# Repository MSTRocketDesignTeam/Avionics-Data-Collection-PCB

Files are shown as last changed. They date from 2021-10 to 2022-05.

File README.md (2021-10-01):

# Overview

This repository contains the PCB design files and accompanying firmware for the Data Collection Board of the S&T Rocket Design Team's SRAD Avionics system.

## Purpose and Motivation
The goal of this project is to create flight-rate PCBs that can collect information about the teams rockets as they are launched.

## Inspirations

Initial developments of this board are to be more or less a direct replacement for a Telemetrum V3, with features and design optimizations to be implemented in future revisions.

A [Telemetrum V3](https://altusmetrum.org/TeleMetrum/) is an amateur rocketry telemetry solution from [Altus Metrum](https://altusmetrum.org/index.html).

[Signal](https://bps.space/signal/) from [BPS.Space](https://bps.space/) is a flight computer first and a data collection solution second. It is designed to stream data to the ground station, although it is likely insufficient for the large 10-30k ft class rockets that our team constructs.

There is also a really cool KiCad tutorial around making a small thumb drive sized pcb with an STM32, RF, and USB components. The link is [here on youtube by Phil's Lab](https://www.youtube.com/watch?v=14_jh3nLSsU) and is a great tutorial on using circuit design software and the process/approach you go through making something like this. Highly recommended to watch and maybe take some notes on, and a pretty solid start for our telemetry board.

# Features

#### Physical

#### Primary Components

#### Sensors

#### Data

#### Power

# Companion Documentation

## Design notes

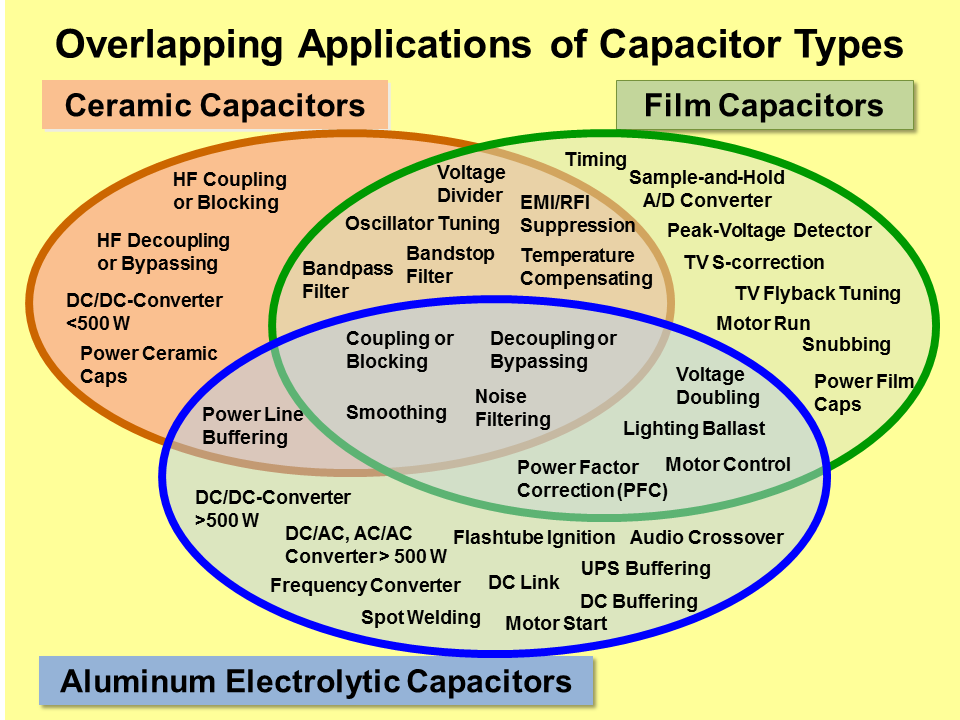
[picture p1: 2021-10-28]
Documentation/Capacitor_Uses.png

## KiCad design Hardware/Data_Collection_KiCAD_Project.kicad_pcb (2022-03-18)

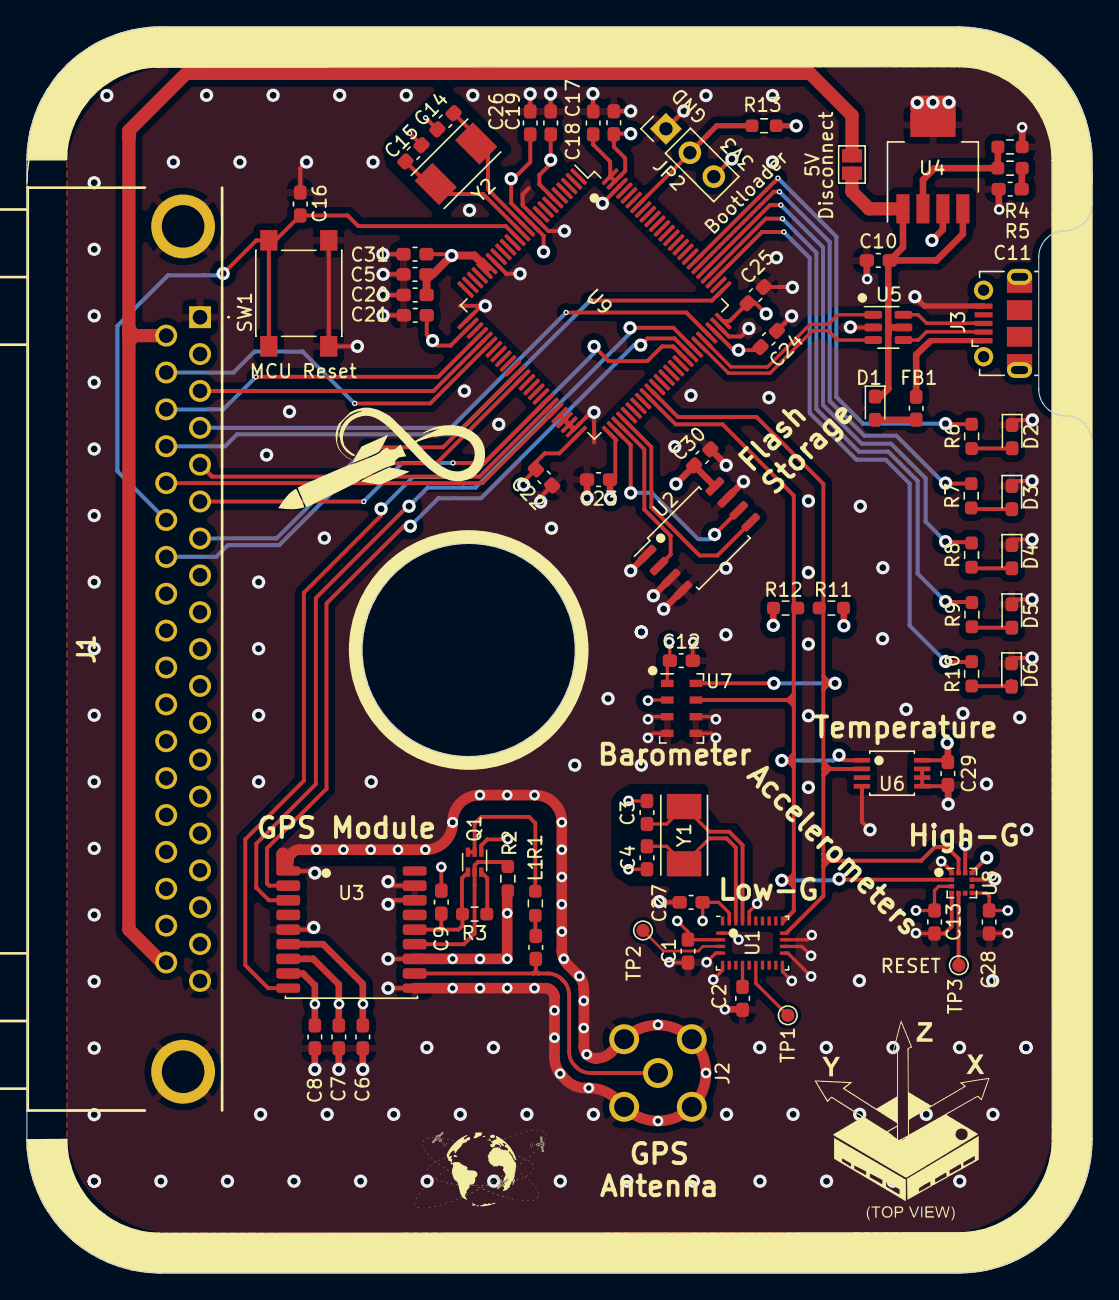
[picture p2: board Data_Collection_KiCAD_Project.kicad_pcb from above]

Board: 4 copper layers, 80.0 x 93.6 mm, 73 parts (0 on the bottom side), 56 nets.

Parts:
C1, C2, C3, C4, C10, C13, C27, C28, C29, C30: 0.1uF; C_0603_1608Metric_Pad1.08x0.95mm_HandSolder
C5, C6, C7, C8, C12, C16, C18, C19, C20, C21, C22, C23, C24, C25: 100nF; C_0603_1608Metric_Pad1.08x0.95mm_HandSolder
C9: 1nF; C_0603_1608Metric_Pad1.08x0.95mm_HandSolder
C11, C17, C26, C31: 1uF; C_0603_1608Metric_Pad1.08x0.95mm_HandSolder
C14, C15: 30pF; C_0603_1608Metric_Pad1.08x0.95mm_HandSolder
D1: D_Schottky_Small; D_0603_1608Metric_Pad1.05x0.95mm_HandSolder
D2, D4, D6: Red; LED_0603_1608Metric_Pad1.05x0.95mm_HandSolder
D3, D5: Grn; LED_0603_1608Metric_Pad1.05x0.95mm_HandSolder
FB1: Ferrite_Bead_Small; C_0603_1608Metric_Pad1.08x0.95mm_HandSolder
J1: L717SDC37P1ACH4F
J2: Conn_Coaxial; SMA_Molex_73251-2200_Horizontal
J3: 10118192-0001LF; USB_Micro-B_Molex-105017-0001
JP1: 5V Disconnect; SolderJumper-2_P1.3mm_Open_Pad1.0x1.5mm
JP2: Debug Jumper; PinHeader_1x03_P2.54mm_Vertical
L1: 27nH; C_0603_1608Metric_Pad1.08x0.95mm_HandSolder
Q1: SI1040X-T1-GE3; SOT-563
R1, R2: 10k; R_0603_1608Metric_Pad0.98x0.95mm_HandSolder
R3: 100k; R_0603_1608Metric_Pad0.98x0.95mm_HandSolder
R4: 390; R_0603_1608Metric_Pad0.98x0.95mm_HandSolder
R5: 240; R_0603_1608Metric_Pad0.98x0.95mm_HandSolder
R6, R7, R8, R9, R10: 820; R_0603_1608Metric_Pad0.98x0.95mm_HandSolder
R11, R12, R13: 4.7k; R_0603_1608Metric_Pad0.98x0.95mm_HandSolder
SW1: MCU Reset; SW_SPST_PTS645
TP1, TP2, TP3: Debug Pad; TestPoint_Pad_D1.0mm
U1: BNO055; LGA-28_5.2x3.8mm_P0.5mm
U2: W25Q32JVSS; SOIC-8_5.23x5.23mm_P1.27mm
U3: MAX-8Q; ublox_MAX
U4: LP38692MPX-ADJ; SOT-223-5
U5: USBLC6-2SC6; SOT-23-6
U6: MIC184YMM-TR
U7: MS5607-02BA; LGA-8_3x5mm_P1.25mm
U8: KX134-1211; LGA-12_2x2mm_P0.5mm
U9: STM32L562VET6Q; LQFP-100_14x14mm_P0.5mm
Y1: 32.768kHz; XTAL_ABM7-32.000MHZ-D2Y-T
Y2: 32MHz; XTAL_ABM7-32.000MHZ-D2Y-T

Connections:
+3V3: C1.2, C5.1, C6.1, C7.1, C8.1, C12.1, C13.1, C17.1, C18.1, C19.1, C20.1, C21.1, C22.1, C23.1, C24.1, C25.1, C26.1, C27.2, C28.1, C29.1, C30.1, C31.1, J1.2, J1.18, JP2.3 (B), R11.2, R12.2, R13.1, U1.3 (VDD), U1.28 (VDDIO), U2.8 (VCC), U3.6 (V_BCKP), U3.7 (VCC_IO), U3.8 (VCC), U4.3 (VOUT), U6.8 (VDD), U7.1 (VDD), U7.2 (PS), U8.3 (IO_VDD), U8.7 (VDD), U8.10 (~CS), U9.6 (VBAT), U9.11 (VDD), U9.20 (VREF+), U9.21 (VDDA), U9.27 (VDD), U9.50 (V15SMPS_1), U9.51 (VDD), U9.73 (VDDUSB), U9.75 (VDD), U9.99 (V15SMPS_2), U9.100 (VDD)
+5V: C10.1, D1.1 (K), JP1.1 (A), U4.1 (EN), U4.4 (VIN), U5.5 (VBUS)
/37 Pin DSUB Bus/Dsub_5v: J1.20, J1.37, JP1.2 (B)
/ABORT_1: J1.7, U9.37 (PE9)
/ABORT_2: J1.26, U9.38 (PE10)
/ALERT_EN: J1.6, U9.43 (PE15)
/ALERT_SCL: J1.5, U9.44 (PB10)
/ALERT_SDA: J1.24, U9.45 (PB11)
/BNO055/~BNO055_BTL: TP2.1, U1.4 (~BOOT_LOAD_PIN)
/BNO055/~BNO055_RESET: TP1.1, U1.11 (~RESET)
/FLASH_CLK: U2.6 (CLK), U9.52 (PB13)
/FLASH_MISO: U2.2 (DO(IO1)), U9.53 (PB14)
/FLASH_MOSI: U2.5 (DI(IO0)), U9.54 (PB15)
/GPS_RX: U3.3 (RXD), U9.69 (PA10)
/GPS_TX: U3.2 (TXD), U9.68 (PA9)
/KX134-1211/KX134_INT1: TP3.1, U8.5 (INT1)
/MAX-8Q/GPS_ANT_NET: J2.1 (In), L1.2, U3.11 (RF_IN)
/MAX-8Q/GPS_LNA_EN: Q1.5 (G1), R2.1, U3.13 (LNA_EN)
/MAX-8Q/GPS_VCC_RF: C9.1, Q1.4 (S2), R3.2, U3.14 (VCC_RF)
/NRST: C16.1, J1.25, SW1.1, U9.14 (NRST)
/SENSOR_SCL: R11.1, U1.19 (COM1), U6.2 (CLK), U7.8 (SCLK), U8.12 (SCLK/SCL), U9.60 (PD13)
/SENSOR_SDA: R12.1, U1.20 (COM0), U6.1 (DATA), U7.7 (SDI/SDA), U8.2 (SDI/SDA), U9.59 (PD12)
/SWCLK: J1.23, U9.76 (PA14)
/SWDIO: J1.4, U9.72 (PA13)
/TELEMETRY_MISO: J1.3, U9.30 (PA6)
/TELEMETRY_MOSI: J1.21, U9.31 (PA7)
/TELEMETRY_SCK: J1.22, U9.29 (PA5)
/USB Connector and ESD/USB_CONN_D+: J3.3, U5.6 (I/O1)
/USB Connector and ESD/USB_CONN_D-: J3.2, U5.4 (I/O2)
/USB_D+: U5.1 (I/O1), U9.71 (PA12)
/USB_D-: U5.3 (I/O2), U9.70 (PA11)
/~GPS_RESET: U3.9 (~RESET), U9.67 (PA8)
GND: C1.1, C2.1, C3.1, C4.1, C5.2, C6.2, C7.2, C8.2, C9.2, C10.2, C11.2, C12.2, C13.2, C14.2, C15.2, C16.2, C17.2, C18.2, C19.2, C20.2, C21.2, C22.2, C23.2, C24.2, C25.2, C26.2, C27.1, C28.2, C29.2, C30.2, C31.2, D2.1 (K), D3.1 (K), D4.1 (K), D5.1 (K), D6.1 (K), J1.1, J1.19, J1.MH1, J1.MH2, J2.2 (Ext), J3.5, JP2.1 (A), Q1.1 (S1), R2.2, R4.2, SW1.2, U1.2 (GND), U1.5 (PS1), U1.6 (PS0), U1.15 (GNDIO), U1.16 (GNDIO), U1.17 (COM3), U1.18 (COM2), U1.25 (GNDIO), U2.1 (~CS), U2.3 (IO2), U2.4 (GND), U2.7 (IO3), U3.1 (GND), U3.5 (EXTINT), U3.10 (GND), U3.12 (GND), U3.16 (SDA), U3.17 (SCL), U4.5 (GND), U5.2 (GND), U6.4 (GND), U6.5 (A2/T1), U6.6 (A1), U6.7 (A0), U7.3 (GND), U7.4 (CSB), U7.5 (CSB), U7.6 (SDO), U8.1 (SDO/ADDR), U8.4 (TRIG), U8.9 (GND), U8.11 (NC), U9.10 (VSS), U9.19 (VREF-/VSSA), U9.26 (VSS), U9.46 (VDDSMPS), U9.47 (VLXSMPS), U9.48 (VSSSMPS), U9.49 (VSS), U9.74 (VSS), U9.98 (VSS)
unnamed: C2.2, U1.9 (CAP)
unnamed: C3.2, U1.26 (XOUT32), Y1.1
unnamed: C4.2, U1.27 (XIN32), Y1.2
unnamed: C11.1, R5.1
unnamed: C14.1, U9.12 (PH0), Y2.1
unnamed: C15.1, U9.13 (PH1), Y2.2
unnamed: D1.2 (A), FB1.1
unnamed: D2.2 (A), R6.1
unnamed: D3.2 (A), R7.1
unnamed: D4.2 (A), R8.1
unnamed: D5.2 (A), R9.1
unnamed: D6.2 (A), R10.1
unnamed: FB1.2, J3.1
unnamed: L1.1, R1.2
unnamed: Q1.2 (D2), Q1.3 (D2), R1.1
unnamed: Q1.6 (D1), R3.1
unnamed: R4.1, R5.2, U4.2 (ADJ)
unnamed: R10.2, U9.78 (PC10)
unnamed: R9.2, U9.79 (PC11)
unnamed: R8.2, U9.80 (PC12)
unnamed: R7.2, U9.81 (PD0)
unnamed: R6.2, U9.82 (PD1)
unnamed: JP2.2 (C), R13.2, U9.94 (PH3)

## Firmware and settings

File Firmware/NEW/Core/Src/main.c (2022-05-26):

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
/* Includes ------------------------------------------------------------------*/
#include "main.h"

 I2C_HandleTypeDef hi2c4;

void SystemClock_Config(void);
static void MX_GPIO_Init(void);
static void MX_I2C4_Init(void);
/**
  * @brief  The application entry point.
  * @retval int
  */
int main(void)
{
  /* USER CODE BEGIN 1 */

	HAL_StatusTypeDef i2c;
	const uint8_t MIC184_ADDR = 0x48 << 1;
	const uint8_t MIC184_CMD_REG = 0x01;
	const uint8_t MS5607_ADDR = 0x77 << 1;
	const uint8_t KX134_ADDR = 0x1E << 1;
	const uint8_t BNO055_ADDR = 0x28 << 1;


	uint8_t buf[1];
	uint8_t tmpBuf[3];
	uint8_t addr;
	uint8_t validAddr[20];
	uint8_t addrIndex = 0;


	/*
	HAL_StatusTypeDef i2c;
	uint8_t buf[1];
	const uint8_t BMP180_ADDR = 0x77 << 1; //7 bit addr?
	*/

  /* USER CODE END 1 */

  /* MCU Configuration--------------------------------------------------------*/

  /* Reset of all peripherals, Initializes the Flash interface and the Systick. */
  HAL_Init();

  /* Configure the system clock */
  SystemClock_Config();

  /* Initialize all configured peripherals */
  MX_GPIO_Init();
  MX_I2C4_Init();
  /* USER CODE BEGIN 2 */

  //Jank i2c scanner
  buf[0] = 0x00;
  i2c = HAL_I2C_Master_Transmit(&hi2c4, MIC184_ADDR, buf, 1, HAL_MAX_DELAY);
  i2c = HAL_I2C_Master_Transmit(&hi2c4, KX134_ADDR, buf, 1, HAL_MAX_DELAY);
  i2c = HAL_I2C_Master_Transmit(&hi2c4, BNO055_ADDR, buf, 1, HAL_MAX_DELAY);
  i2c = HAL_I2C_Master_Transmit(&hi2c4, MS5607_ADDR, buf, 1, HAL_MAX_DELAY);

  //initialize array to 0
  	  for (uint8_t i = 0; i < 20; i++){
  		  validAddr[i] = 0;
  	  }

  	  for (uint8_t i = 0; i < 127; i++){
  		  buf[0] = 0x00;
  		  uint8_t x = i << 1;
  		  i2c = HAL_I2C_Master_Transmit(&hi2c4, x, buf, 1, HAL_MAX_DELAY);
  		  HAL_Delay(1);
  		  if ((i2c != HAL_ERROR) && (addrIndex < 20)){
  			  validAddr[addrIndex] = i;
  			  addrIndex++;
  		  }
  	  }

  	  while (1){
  		;
  	  }

  /* USER CODE END 2 */

  /* Infinite loop */
  /* USER CODE BEGIN WHILE */
  while (1)
  {
    /* USER CODE END WHILE */

    /* USER CODE BEGIN 3 */



	  /*
	  HAL_GPIO_WritePin(GPIOC, GPIO_PIN_10, GPIO_PIN_SET);
	  //buf[0] = 0xD0;
	  //i2c = HAL_I2C_Master_Transmit(&hi2c4, BMP180_ADDR, buf, 1, HAL_MAX_DELAY);
	  //i2c = HAL_I2C_Master_Receive(&hi2c4, BMP180_ADDR, buf, 1, HAL_MAX_DELAY);

	  //send the command reg addr to the MIC184
	  tmpBuf[0] = 0x01;
	  i2c = HAL_I2C_Master_Transmit(&hi2c4, MIC184_ADDR, tmpBuf, 1, HAL_MAX_DELAY);
	  HAL_Delay(50);
	  i2c = HAL_I2C_Master_Receive(&hi2c4, MIC184_ADDR, tmpBuf, 2, HAL_MAX_DELAY);

	  //KX134-1211
	  //check WHOAMI register
	  tmpBuf[0] = 0x13;
	  i2c = HAL_I2C_Master_Transmit(&hi2c4, KX134_ADDR, tmpBuf, 1, HAL_MAX_DELAY);
	  i2c = HAL_I2C_Master_Receive(&hi2c4, KX134_ADDR, tmpBuf, 1, HAL_MAX_DELAY);



	  //MS5607
	  //reset the chip
	  tmpBuf[0] = 0x1E;
	  i2c = HAL_I2C_Master_Transmit(&hi2c4, MS5607_ADDR, tmpBuf, 1, HAL_MAX_DELAY);
	  HAL_Delay(50);
	  //start temp convert
	  tmpBuf[0] = 0x58;
	  i2c = HAL_I2C_Master_Transmit(&hi2c4, MS5607_ADDR, tmpBuf, 1, HAL_MAX_DELAY);
	  HAL_Delay(50);
	  //trigger ADC Read
	  tmpBuf[0] = 0x00;
	  i2c = HAL_I2C_Master_Transmit(&hi2c4, MS5607_ADDR, tmpBuf, 1, HAL_MAX_DELAY);
	  HAL_Delay(50);
	  i2c = HAL_I2C_Master_Receive(&hi2c4, MS5607_ADDR, tmpBuf, 3, HAL_MAX_DELAY);
	  */
	  /*
	  buf[0] = 0xD0; //chip ID reg
	  i2c = HAL_I2C_Master_Transmit(&hi2c4, BMP180_ADDR, buf, 1, HAL_MAX_DELAY);
	  i2c = HAL_I2C_Master_Receive(&hi2c4, BMP180_ADDR, buf, 1, HAL_MAX_DELAY);
	  HAL_Delay(500);
	  if (i2c == HAL_OK){
		  HAL_GPIO_WritePin(GPIOC, GPIO_PIN_10, GPIO_PIN_RESET);
	  }
	  HAL_Delay(500);
	  */
	  //HAL_GPIO_WritePin(GPIOC, GPIO_PIN_10, GPIO_PIN_RESET);
	  //HAL_Delay(50);





	  //HAL_GPIO_TogglePin(GPIOC, GPIO_PIN_11);
	  //HAL_Delay(100);
	 // HAL_GPIO_TogglePin(GPIOC, GPIO_PIN_10);
	  //HAL_GPIO_WritePin(GPIOC, GPIO_PIN_11, GPIO_PIN_SET);
	  //HAL_GPIO_WritePin(GPIOC, GPIO_PIN_10, GPIO_PIN_SET);

	  //Begin Jank Test Code
	  //start a pressure conversion
	  //MS5607_Pressure[0] = MS5607_D1_REG;
	  //i2c = HAL_I2C_Master_Transmit(&hi2c3, MS5607_ADDR, MS5607_Pressure, 1, HAL_MAX_DELAY); //transmit to start D1 4096 OSR convert
	  //if (i2c != HAL_OK){
		//  HAL_GPIO_WritePin(GPIOC, GPIO_PIN_12, GPIO_PIN_SET);
	  //}

	  //HAL_Delay(100);

	  //start an adc conversion
	  //MS5607_Pressure[0] = MS5607_ADC_REG;
	  //i2c = HAL_I2C_Master_Transmit(&hi2c4, MS5607_ADDR, MS5607_Pressure, 1, HAL_MAX_DELAY);
	  //if (i2c != HAL_OK){
		//  HAL_GPIO_WritePin(GPIOD, GPIO_PIN_0, GPIO_PIN_SET);
	  //}

	  //HAL_Delay(100);

	  //read 24 bit value
	  //i2c = HAL_I2C_Master_Receive(&hi2c4, MS5607_ADDR, MS5607_Pressure, 3, HAL_MAX_DELAY);

	  //End Jank Test Code
  }
  /* USER CODE END 3 */
}

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


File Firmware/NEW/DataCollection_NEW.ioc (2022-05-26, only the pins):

Mcu.UserName=STM32L562VETxQ
PC10.Signal=GPIO_Output
PC11.Signal=GPIO_Output
PC12.Signal=GPIO_Output
PD0.Signal=GPIO_Output
PD12.Signal=I2C4_SCL
PD13.Signal=I2C4_SDA

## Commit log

2021-10-01 Schematic v1.0.0
    Creation of KiCAD project file, initial draft of PCB schematic file, components chosen as a starting point and will likely be altered in future revisions.
    [Data_Collection_KiCAD_Project.kicad_pcb, Data_Collection_KiCAD_Project.sch]
2021-10-01 Schematic v1.0.1
    Organized schematic into separate sheets. This helps modularize the project and eases switching between components as the design progresses.
    [BAROMETER_MS5607-02.sch, Data_Collection_KiCAD_Project.sch, FLASH_W25Q32JV.sch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]
2021-10-01 Schematic v1.0.2
    Moved MCU to separate sheet.
    [BAROMETER_MS5607-02.sch, Data_Collection_KiCAD_Project.sch, FLASH_W25Q32JV.sch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]
2021-10-03 Schematic v1.0.3
    Reorganized the main page to use bus lines.
    [BAROMETER_MS5607-02.sch, Data_Collection_KiCAD_Project.sch, FLASH_W25Q32JV.sch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]
2021-10-03 Schematic v1.0.4
    Added I2C addresses to MEMS, Temp Sensor, and Barometer on main schematic page.
    [BAROMETER_MS5607-02.sch, Data_Collection_KiCAD_Project.sch, FLASH_W25Q32JV.sch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]
2021-10-11 Schematic v1.0.5
    Added 64G capable Accelerometer.
    Replaced ICM-20948 with BNO055 for 3.3V I2C compatibility.
    Things to do: Add I2C pullup resistors for entire bus, Route INT pins to uC.
    [Data_Collection_KiCAD_Project.sch, IMU.sch, MCU_L552CC.sch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]
2021-10-13 Re-Added MEMS_ICM-20948.sch
    Re-added schematic file in case there is need in the future.
    [MEMS_ICM-20948.sch]
2021-10-13 Separated BNO055 and KX134
    Separated the hierarchical sheets for the BNO055 IMU and KX134 High G-Accelerometer.
    [BAROMETER_MS5607-02.sch, Data_Collection_KiCAD_Project.sch, FLASH_W25Q32JV.sch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]
2021-10-13 Starting Assigning Pins and Messed with Crystal Scalers
    - Started to pin physical pin assignments in the pinout view to show a graphical representation of which pins are available.
    - Enabled the high speed external crystal and configured PLL scalers to create a 48MHz signal for USB and 96MHz signal for main core. (if power consumption is an issue we can change this)
    [Avionics-Data-Collection-STM32_Project.ioc, main.c]
2021-10-28 Formatting
    Misc Formatting and CubeIDE configuration.
    Also Added datasheets folder
    [BAROMETER_MS5607-02.sch, Data_Collection_KiCAD_Project.sch, FLASH_W25Q32JV.sch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]
2021-11-01 Added Main Bus Layout
    added main bus connector and connected various pins
    TODO:
    -Implement I2C interrupt pin
    -Add I2C Pullups
    -Add I2C Capacitors
    -Check for auxiliary pins needed from sensors
    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
    [Data_Collection_KiCAD_Project.sch, USB_ESD.sch]
2021-11-03 Added Power Budget Spreadsheet
    -Add power buffer cap and diode?
    -Double check and finalize layouts
    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
    [BAROMETER_MS5607-02.sch, DataCollection_PowerBudget.xlsx, Data_Collection_KiCAD_Project.sch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]
2021-11-17 Added Main Bus Card Edge Connector Sheet
    [BAROMETER_MS5607-02.sch, Data_Collection_KiCAD_Project.sch, FLASH_W25Q32JV.sch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]
2021-11-18 Fixed Component Libraries
    Changed over from project specific to global libraries.
    [BAROMETER_MS5607-02.sch, Data_Collection_KiCAD_Project.sch, FLASH_W25Q32JV.sch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]
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2021-11-23 Added Resistors for LED
    [MCU_L552CC.sch]
2021-11-24 footprint and value changes
    [BAROMETER_MS5607-02.sch, Data_Collection_KiCAD_Project.sch, FLASH_W25Q32JV.sch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]
2021-11-24 Added 37Pin DSUB Main Bus
    [BAROMETER_MS5607-02.sch, Data_Collection_KiCAD_Project.sch, FLASH_W25Q32JV.sch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]
2021-11-24 Corrected Main Bus Connector
    [Data_Collection_KiCAD_Project.sch, file61A437B4.sch]
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2021-12-01 Changed MCU and started pcb
    [DSUB.sch, Data_Collection_KiCAD_Project.kicad_pcb, Data_Collection_KiCAD_Project.sch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]
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2021-12-02 Finished laying out PCB Components
    [Data_Collection_KiCAD_Project.kicad_pcb]
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2021-12-07 GPS layout change and test point tweaks
    [BAROMETER_MS5607-02.sch, DSUB.sch, Data_Collection_KiCAD_Project.kicad_pcb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]
2021-12-07 Finalized
    Everything is routed. There are probably some things that need rerouting or adjustment.
    [DSUB.sch, Data_Collection_KiCAD_Project.kicad_pcb]
2021-12-21 Schematic Tweaks and Board Dimensioned
    [BAROMETER_MS5607-02.sch, DSUB.sch, Data_Collection_KiCAD_Project.kicad_pcb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]
2021-12-21 routing progress and pin reassignment
    [DSUB.sch, Data_Collection_KiCAD_Project.kicad_pcb, Data_Collection_KiCAD_Project.sch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]
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2022-01-24 Updated file format to KiCAD v6, replaced voltage regulator
    [BAROMETER_MS5607-02.kicad_sch, DSUB.kicad_sch, Data_Collection_KiCAD_Project.kicad_pcb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]
2022-01-24 Added 3D models to components
    [Data_Collection_KiCAD_Project.kicad_pcb, Data_Collection_KiCAD_Project.kicad_sch, MCU_STM32L562VET6Q.kicad_sch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]
2022-01-24 Updated MCU Component Sheet
    Used the file from the Telemetry board for compatibility and commonality.
    [Data_Collection_KiCAD_Project.kicad_pcb, Data_Collection_KiCAD_Project.kicad_sch, FLASH_W25Q32JV.kicad_sch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]
2022-01-24 Corrected PCB edge cuts, removed components
    Will be mimicking layout done by Seth Sievers
    [BAROMETER_MS5607-02.kicad_sch, DSUB.kicad_sch, Data_Collection_KiCAD_Project.kicad_sch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]
2022-01-25 Organized components, arranged filter caps
    [BAROMETER_MS5607-02.kicad_sch, DSUB.kicad_sch, Data_Collection_KiCAD_Project.kicad_pcb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]
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2022-01-25 Added signatures to silkscreen
    [Data_Collection_KiCAD_Project.kicad_pcb]
2022-01-28 wtf is wrong with my github install
    [BAROMETER_MS5607-02.kicad_sch, BAROMETER_MS5607-02.sch, DSUB.kicad_sch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]
2022-01-29 fixed it
    [BAROMETER_MS5607-02.kicad_sch, BAROMETER_MS5607-02.sch, DSUB.kicad_sch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]
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2022-01-30 Replaced Temp Sense and finalized routing
    [Data_Collection_KiCAD_Project.kicad_pcb, Data_Collection_KiCAD_Project.kicad_sch, GNSS_MAX-8Q.kicad_sch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]
2022-01-30 I think it is done....
    maybe
    hopefully
    please
    [Data_Collection_KiCAD_Project.kicad_pcb, Data_Collection_KiCAD_Project.kicad_sch, TEMPSENSOR_MIC184YMM.kicad_sch]
2022-01-31 Corrected Si-1040X Footprint
    Canged from TSOT-23-6 to SOT-563 (Called SC-89-6 in datasheet)
    [Data_Collection_KiCAD_Project.kicad_pcb]
2022-01-31 Improved data line separation, added ground stitching vias
    [Data_Collection_KiCAD_Project.kicad_pcb]
2022-01-31 Added silkscreen art, adjusted copper pour clearances
    [Data_Collection_KiCAD_Project.kicad_pcb]
2022-01-31 Added more silkscreen art
    [Data_Collection_KiCAD_Project.kicad_pcb]
2022-01-31 Corrected Si1040X Footprint
    [Data_Collection_KiCAD_Project.kicad_sch, GNSS_MAX-8Q.kicad_sch]
2022-02-01 fixed broken layer fill
    pad was unconnected due to DRC violation due to copper pour keep out zone.
    [Data_Collection_KiCAD_Project.kicad_pcb]
2022-02-07 Corrected silkscreen qr code
    [Data_Collection_KiCAD_Project.kicad_pcb]
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2022-02-19 Previous change
    didnt push, so now i am
    [Data_Collection_KiCAD_Project.kicad_pcb]
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2022-02-28 Corrected Board Edge Cuts
    [Data_Collection_KiCAD_Project.kicad_pcb]
2022-02-28 Aligned components to new board dimensions, adjusted silkscreen border, aligned center hole
    Some traces need to be corrected around the center hole still
    [Data_Collection_KiCAD_Project.kicad_pcb]
2022-02-28 Added dimensions for center hole to user drawings layer
    [Data_Collection_KiCAD_Project.kicad_pcb]
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2022-03-02 Optimized spacings, via stitching, added right angle sma w/ male
    [Data_Collection_KiCAD_Project.kicad_pcb]
2022-03-05 Adjusted component spacing, corrected MCU schematic, added cutout for USB, moved SMA inwards
    [Data_Collection_KiCAD_Project.kicad_pcb, Data_Collection_KiCAD_Project.kicad_sch, MCU_L562VE.kicad_sch]
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2022-03-18 Generated gerb
    Gerb and drill files were generated
    [Data_Collection_KiCAD_Project.kicad_pcb]
2022-03-18 updated board and gerbs
    JLC didnt like our stuff so landmarks were changed to account for this.
    [Data_Collection_KiCAD_Project.kicad_pcb]

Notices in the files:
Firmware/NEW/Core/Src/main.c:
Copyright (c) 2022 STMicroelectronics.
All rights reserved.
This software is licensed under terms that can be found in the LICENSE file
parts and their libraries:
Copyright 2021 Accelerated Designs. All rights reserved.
